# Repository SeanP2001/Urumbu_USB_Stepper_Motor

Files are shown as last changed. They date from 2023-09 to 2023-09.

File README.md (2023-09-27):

# Urumbu USB Stepper Motor

**This Project follows on from the work of Professor Neil Gershenfeld, Quentin Bolsee and Rob Hart at MIT. [Here](https://gitlab.cba.mit.edu/neilg/urumbu) is the original repository.**

## Table of Contents <!-- omit from toc -->

- [Introduction](#introduction)
- [Brief](#brief)
- [Design Aims](#design-aims)
- [PCB Design](#pcb-design)
- [Manufacturing](#manufacturing)
- [Programming](#programming)
  - [Flashing SAMD11 Firmware](#flashing-samd11-firmware)
  - [Adding the Arduino IDE Board Manager](#adding-the-arduino-ide-board-manager)
  - [The Arduino Code](#the-arduino-code)
  - [The Test Code](#the-test-code)
- [Motor Module Characteristics](#motor-module-characteristics)
  - [Current Draw](#current-draw)
  - [Motor Speed](#motor-speed)
  - [Motor Torque](#motor-torque)
- [Using the Module](#using-the-module)
- [Conclusion](#conclusion)
- [Further Work](#further-work)

## Introduction

In the final year of my Bachelors degree I completed a dissertation. This repository is a summary of that work. Included in the repository is all of the information and files to reproduce and use the modules which I designed.

Bangor FabLAB needed to develop methods to teach the Fab Academy curriculum. The curriculum includes two weeks of making machines that move. Students have a very limited time to complete these projects and so they needed a flexible framework which could be used to rapidly prototype motion systems.

Traditional motion systems have all of the components plugged into the controller board. This board has firmware code to control all of the components. While prototyping, it is common to want to add parts like extra motors or switches. With this approach, the controller board must be re-designed, manufactured and programmed. This is time-consuming, creates waste, breaks the creative flow, and requires substantial skills. Students only have one week to do their projects, and this approach is not suitable.

Professor Neil Gershenfeld and his colleagues Quentin Bolsee and Rob Hart have developed a modular solution to this problem called [Urumbu](https://gitlab.cba.mit.edu/neilg/urumbu). These modules are designed to plug into a computer via a USB port. The modules move in response to serial communications from the connected computer. To add more motors to an Urumbu-based machine, the user simply plugs another motor module into the PC and adds it to their code. This is much quicker and does not break the creative flow.

## Brief

I was tasked with equipping the FabLAB to teach the machine building exercises. This involved...
- Adapting the Urumbu design to meet our requirements.
- Manufacturing a set of modules.
- Testing and documenting the module characteristics to understand their capabilities.
- Demonstrating their use through building a motion system. 

## Design Aims

The original design used a DRV8428 motor driver. This motor driver causes the motor to generate noise. This driver is also surface-mount and so if the driver were to fail mid-project, it would be difficult and time-consuning to replace. 

With these issues in mind, I aimed to design a module with the following characteristics:
- Use a silent, user replaceable stepper motor driver (TMC2208, StepStick socketed package).
- Able to be mounted to the back of a NEMA 14 motor.
- Able to be manufactured in the FabLAB using their isolation milling process with FR1 board.

## PCB Design

After three breadboard prototypes and six circuit board revisions I arrived at this design.

The top section is the power section which takes the five volts from the USB connection and steps it down to a stable 3.3 volts for the microcontroller. The main use for the SAMD microcontroller is to interpret the information from the USB data lines and send the correct direction and step signals to the motor driver. The motor driver connects to the four motor pins and pulses them in sequence to advance the motor whenever it receives a step signal.

<p align="center">
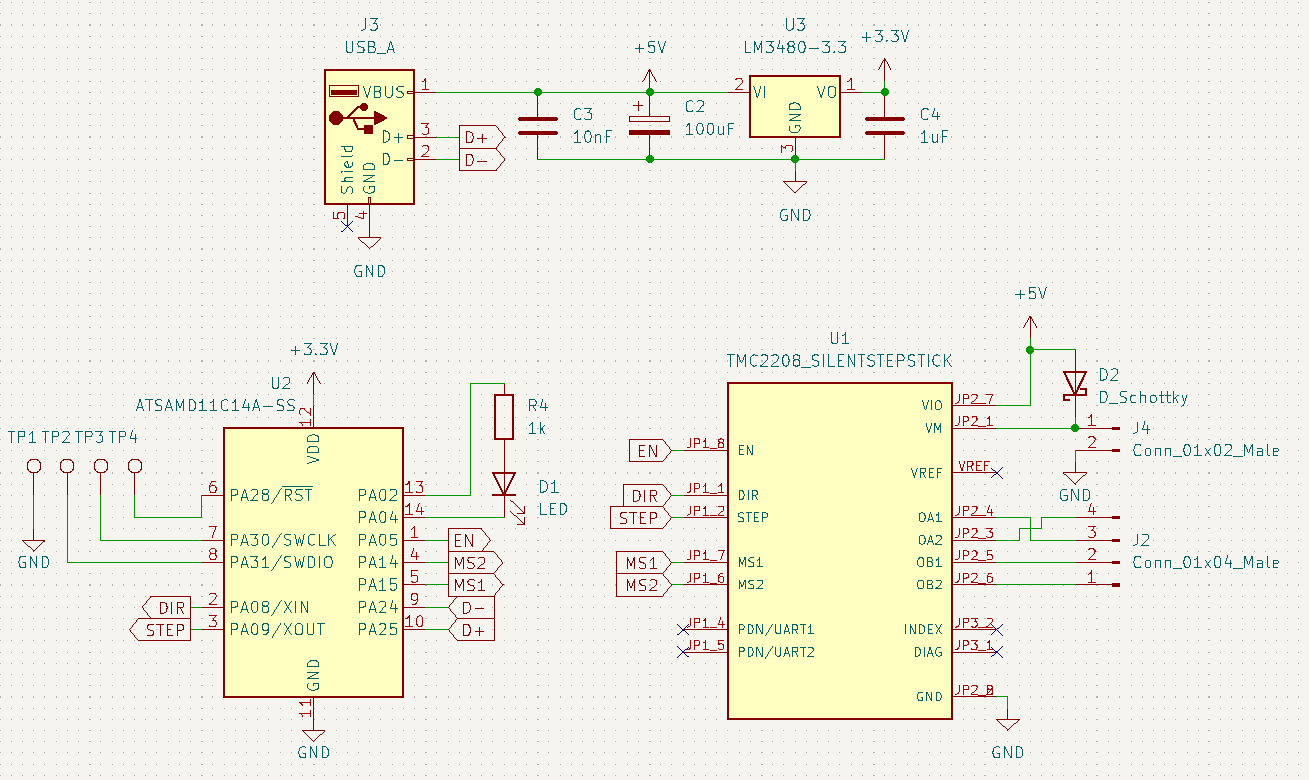
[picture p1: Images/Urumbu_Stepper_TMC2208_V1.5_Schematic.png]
  
</p>

<p align="center">
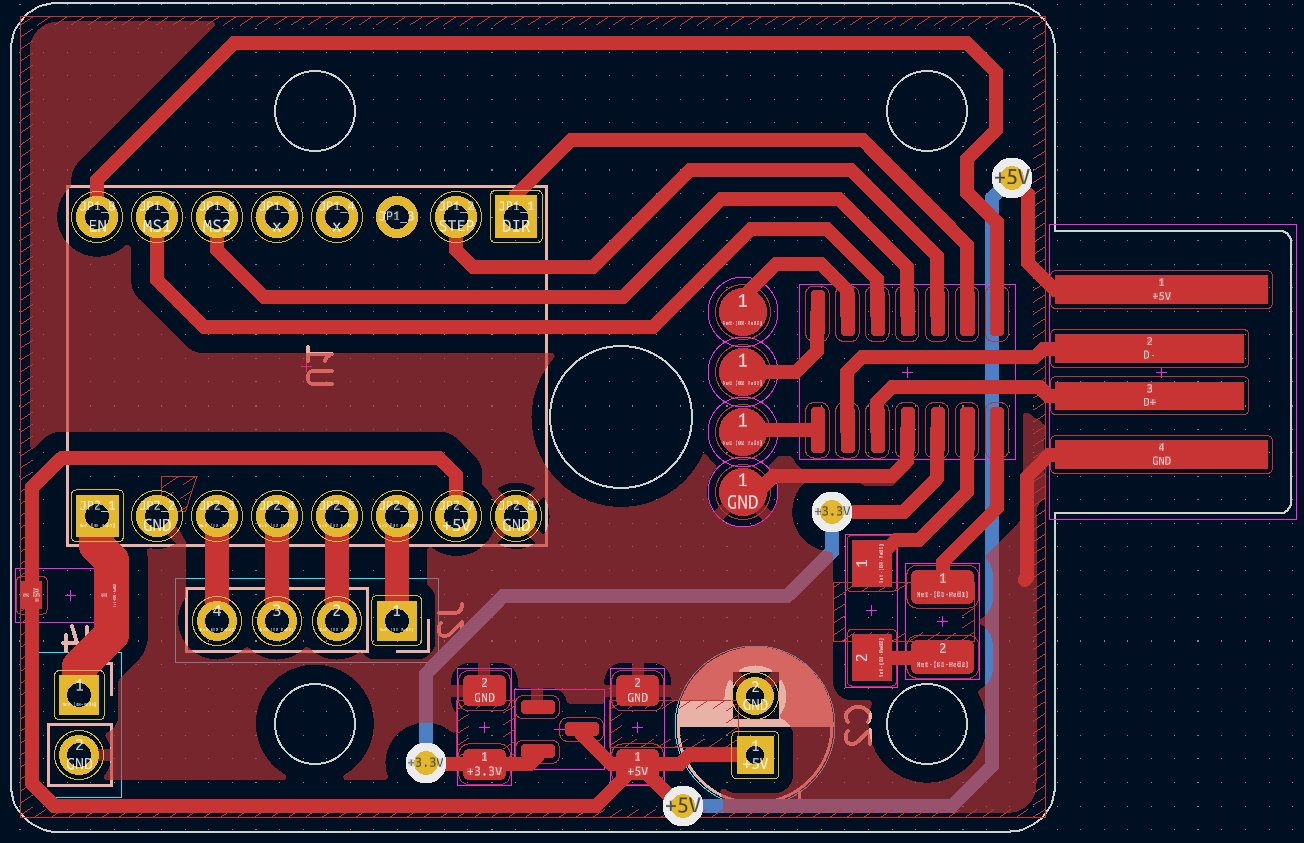
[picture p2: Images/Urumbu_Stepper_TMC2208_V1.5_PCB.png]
  
</p>

## Manufacturing

Images of the PCB were exported from KiCAD. Using [modsproject](https://modsproject.org/), these images were converted into toolpaths and saved in `./PCB_Design/Toolpaths`. Using the Roland SRM-20 CNC mill with a 0.4mm end mill, the traces were isolation milled out of a copper-clad FR1 board. A 0.7mm end mill was then used to drill the holes and cut the board outline. The components were soldered by hand using a soldering iron, as this is the best method for FR1 boards.

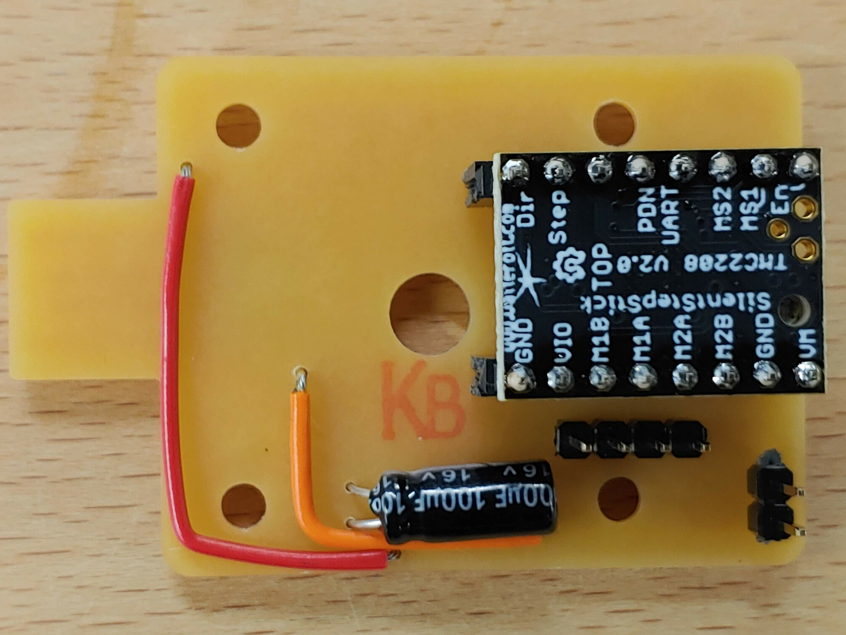
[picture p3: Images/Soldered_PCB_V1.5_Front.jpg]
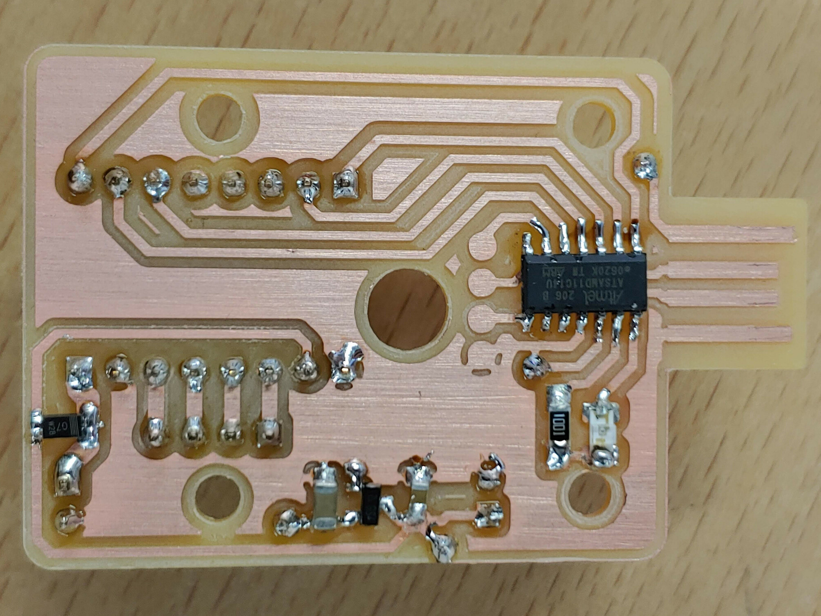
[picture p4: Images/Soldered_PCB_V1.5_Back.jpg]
|   |  |
| --- | --- |

## Programming

### Flashing SAMD11 Firmware

The ["ArduinoCore"](https://github.com/mattairtech/ArduinoCore-samd/blob/master/bootloaders/zero/binaries/sam_ba_Generic_D11C14A_SAMD11C14A.bin) firmware was loaded on to the SAMD11 microcontroller to allow it to be programmed via USB. To do this, I used an Atmel-ICE programmer with the "mini-squid" cable and connected it to the microcontroller in the following way:

| SAM Programming Header Pin Number | Function | SAMD11C Pin Number |
| --- | --- | --- |
| 1 | VREF | 12 |
| 2 | DIO | 8 |
| 3 | GND | 11 |
| 4 | CLK | 7 |
| 5 | GND | 11 |
| 6 | Not Connected | |
| 7 | Not Connected | |
| 8 | Not Connected | |
| 9 | GND | 11 |
| 10 |RST | 6 |

I used a crocodile clip to connect the ground connections to the ground plane. The voltage reference pin was connected via a test clip to the 3V jumper wire on the circuit board. The other connections were connected to a pogo-pin board which was held against the programming pads when the board was being programmed. The board recieved power through the USB connection. 

<p align="center">
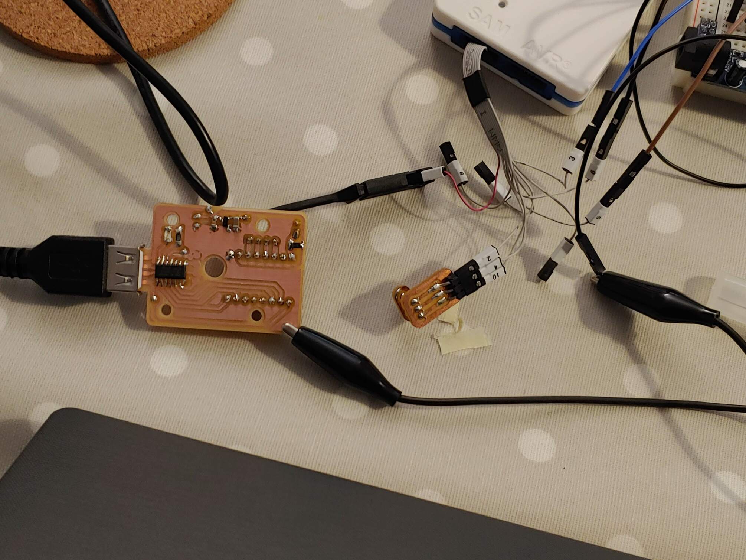
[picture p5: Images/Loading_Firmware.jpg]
  
</p>

Atmel Studio was used to load the firmware onto the microcontroller. While holding the pogo pins to the pads, I selected `Device Programming > Apply` and the device was successfully connected to. On the "Memories" tab I selected the [firmware file](https://github.com/mattairtech/ArduinoCore-samd/blob/master/bootloaders/zero/binaries/sam_ba_Generic_D11C14A_SAMD11C14A.bin) and clicked "Apply" to write the firmware to the microcontroller.

<p align="center">
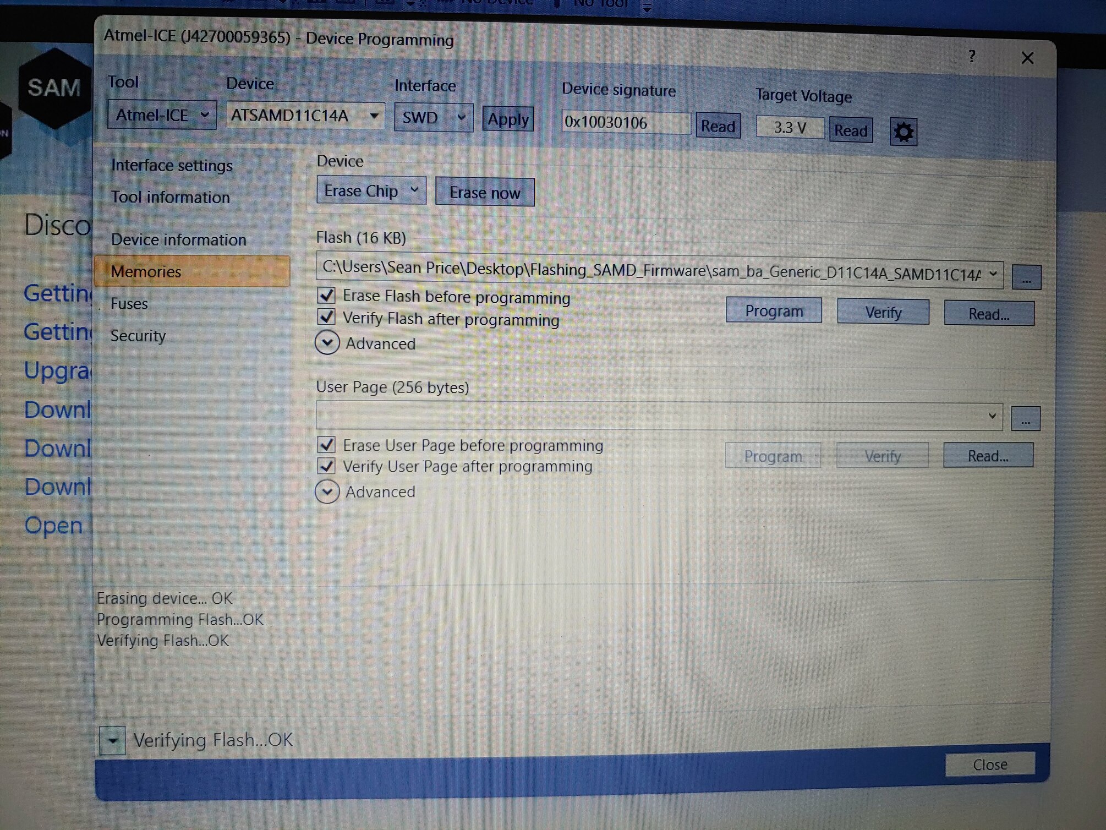
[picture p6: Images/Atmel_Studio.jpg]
  
</p>

### Adding the Arduino IDE Board Manager

The [Fab SAM board manager](https://raw.githubusercontent.com/qbolsee/ArduinoCore-fab-sam/master/json/package_Fab_SAM_index.json) was added to the Arduino IDE, following the [MIT guide](https://mtm.cba.mit.edu/2021/2021-10_microcontroller-primer/fab-arduino/). This allowed the Arduino IDE to be used to program the SAMD11C on the PCB.

### The Arduino Code

The Arduino code running on the Urumbu modules was very heavily inspired by the [original “serialstep” code](https://gitlab.cba.mit.edu/neilg/urumbu/-/tree/master/serialstep/serialstep.ino) used at MIT. The premise of the code is to continuously check whether any serial data has been sent via the USB connection. If the received data is an ’f’, the stepper motor will step clockwise (forwards). If the received data is an ’r’, the stepper motor will step anti-clockwise (reverse).

<p align="center">
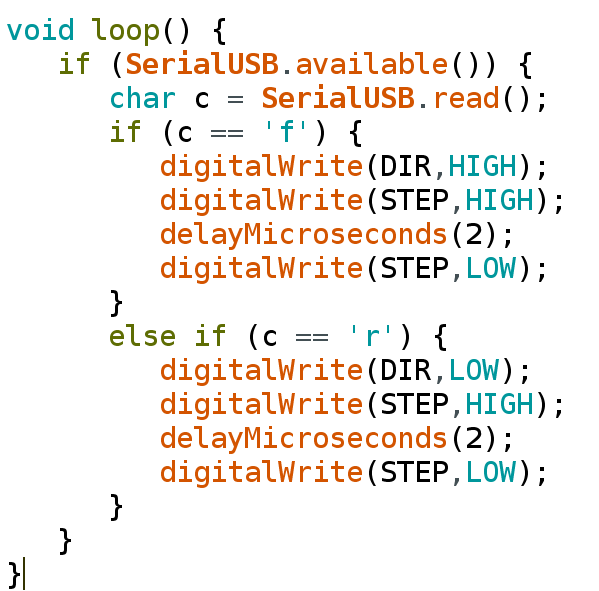
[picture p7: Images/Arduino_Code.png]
  
</p>

### The Test Code

The `./Test_Code/SerialStepControllerTest.py` code sends 'f' and 'r' characters via USB to the motor module to turn the shaft one rotation clockwise and then anti-clockwise repeatedly.

<p align="center">
  
</p>

The `./Test_Code/SerialStepKeyboardControllerTest.py` code sends 'f' and 'r' characters via USB to the motor module to turn the shaft in response to the user pressing the arrow keys on the PC.

<p align="center">
  
</p>

## Motor Module Characteristics

These documented characteristics should help anybody aiming to use these modules by giving them the information to assess whether these modules are capable of fulfilling their requirements.

### Current Draw

| Motor State | Lowest Current Draw (A) | Highest Current Draw (A) | Average Current Draw (A) | 
| --- | --- | --- | --- |
| Idle | 0.13 | 0.19 | 0.16 |
| Moving | 0.31 | 0.37 | 0.34 |
| Moving with 5Ncm Load | 0.31 | 0.37 | 0.34 |

### Motor Speed

The maximum speed of the motor is approximately 2.64 revolutions per second or 158.5 revolutions per minute.

### Motor Torque

The motor was able to lift a mass of 100g at a distance of 6.8cm from the motor shaft. This gives a torque figure of 6.67Ncm.

## Using the Module

I then went on to demonstrate the use of these modules and test that they functioned as expected. To do this I designed, manufactured and programmed a crane motion system. [Here](https://github.com/SeanP2001/Urumbu_Crane) is the repository for that project.

<p align="center">
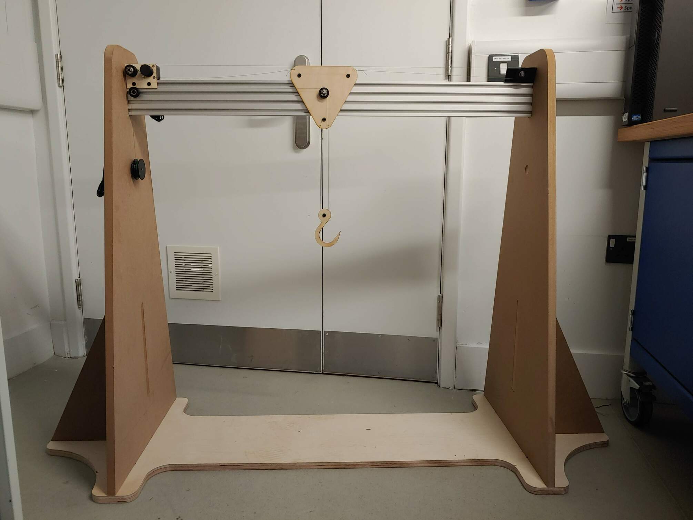
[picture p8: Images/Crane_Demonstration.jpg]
  
</p>

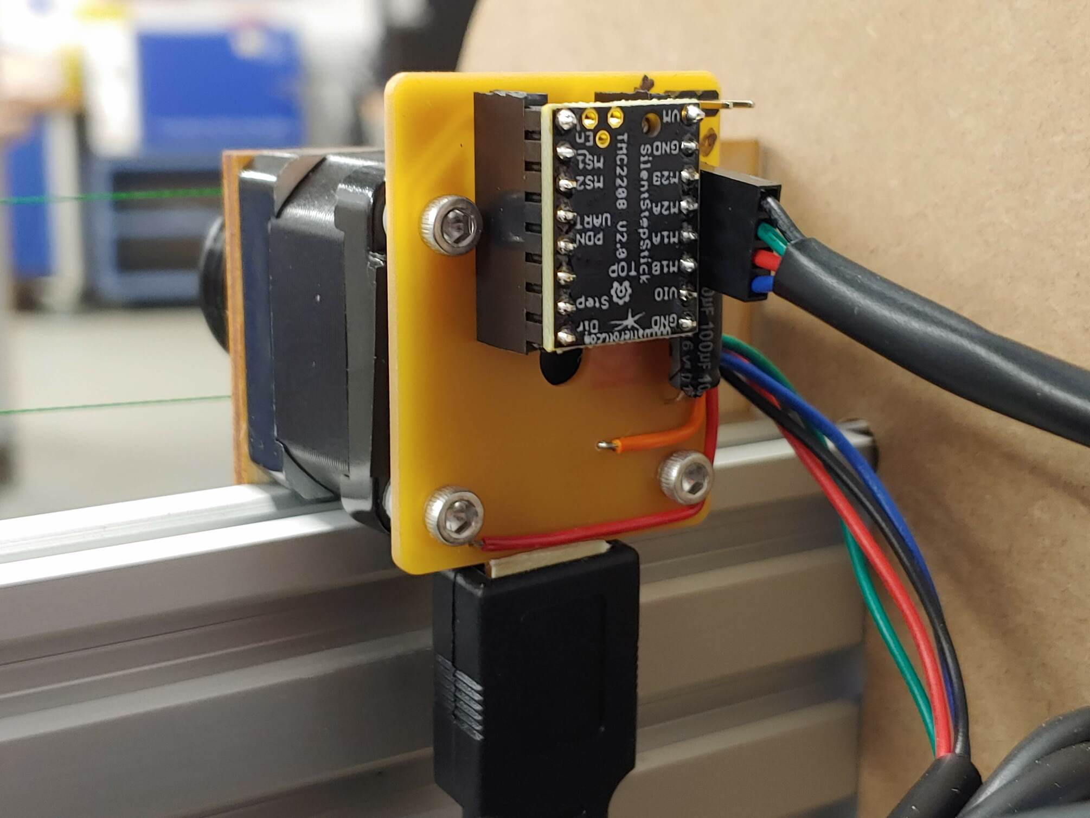
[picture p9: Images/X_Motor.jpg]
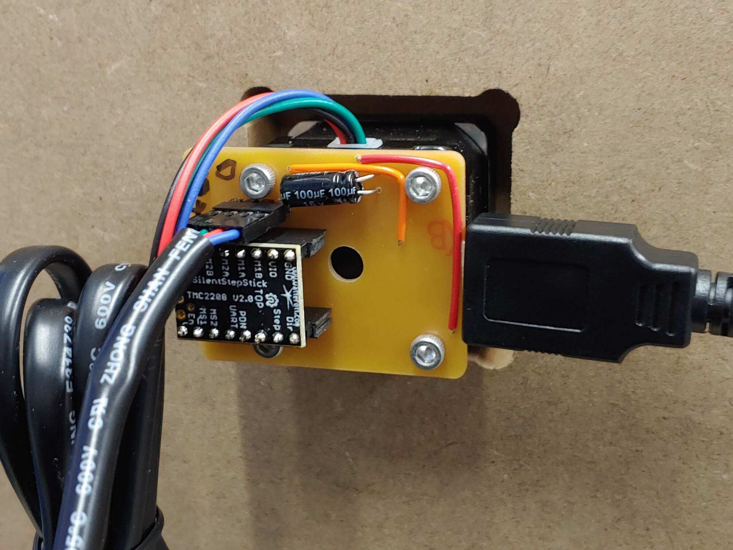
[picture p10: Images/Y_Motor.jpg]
|   |  |
| --- | --- |

## Conclusion

In conclusion, I designed a set of stepper motor Urumbu modules to use a silent, user-replaceable motor driver. A set of modules was manufactured using standard FabLAB tools and parts. The current draw, speed and torque of the motor modules were tested and documented for future students to reference. I also designed and built a motion system to demonstrate the use of these modules. Overall this project was a success. The modules met the brief and will soon be used by Fab Academy students.

## Further Work

There are a few aspects of this project which could be furnter developed:
- Design more modules
  - Button Interface (Controller)
  - Limit Switch
  - LCD
- Write a Python Library to simplify the controller code that students need to write. They could use simple functions to control the modules, rather than dealing with the specifics of the serial communications and distance calculations.

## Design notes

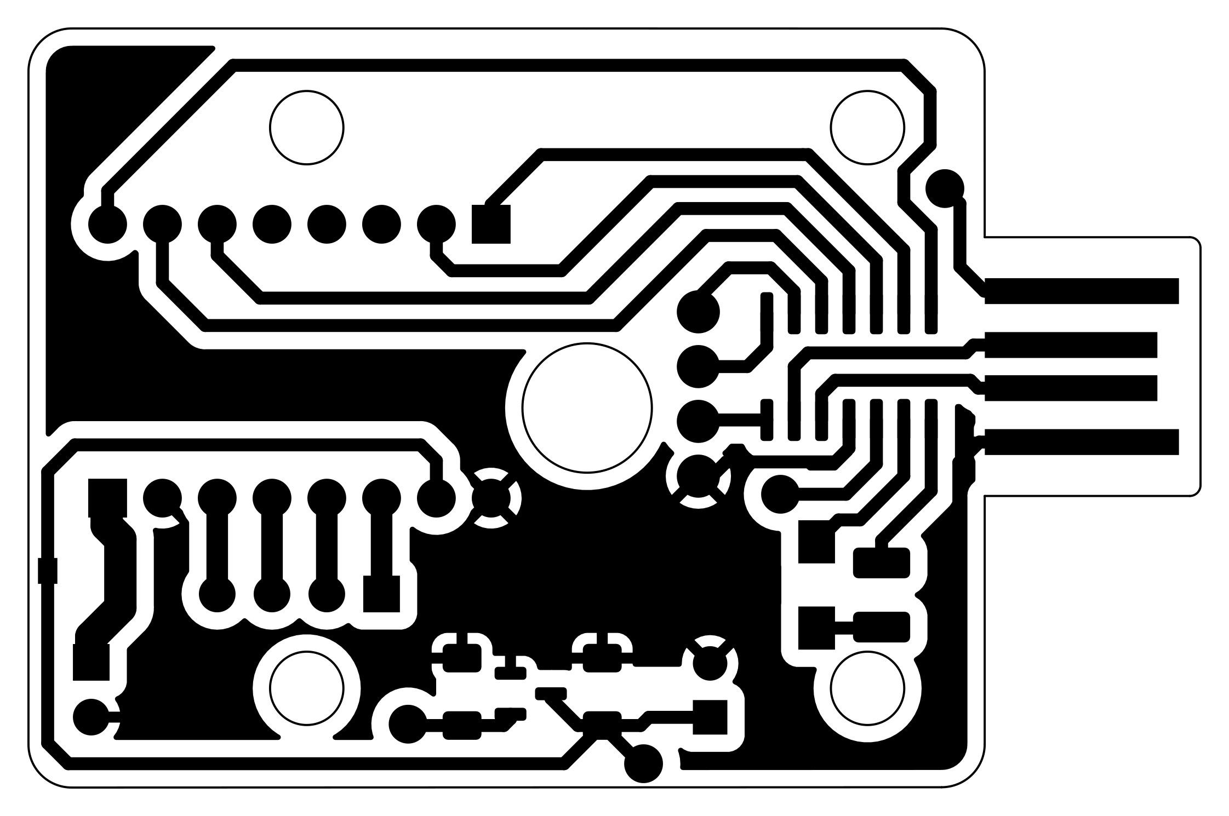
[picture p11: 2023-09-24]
PCB_Design/SVG_Out/Urumbu_Stepper_TMC2208-F_Cu.png

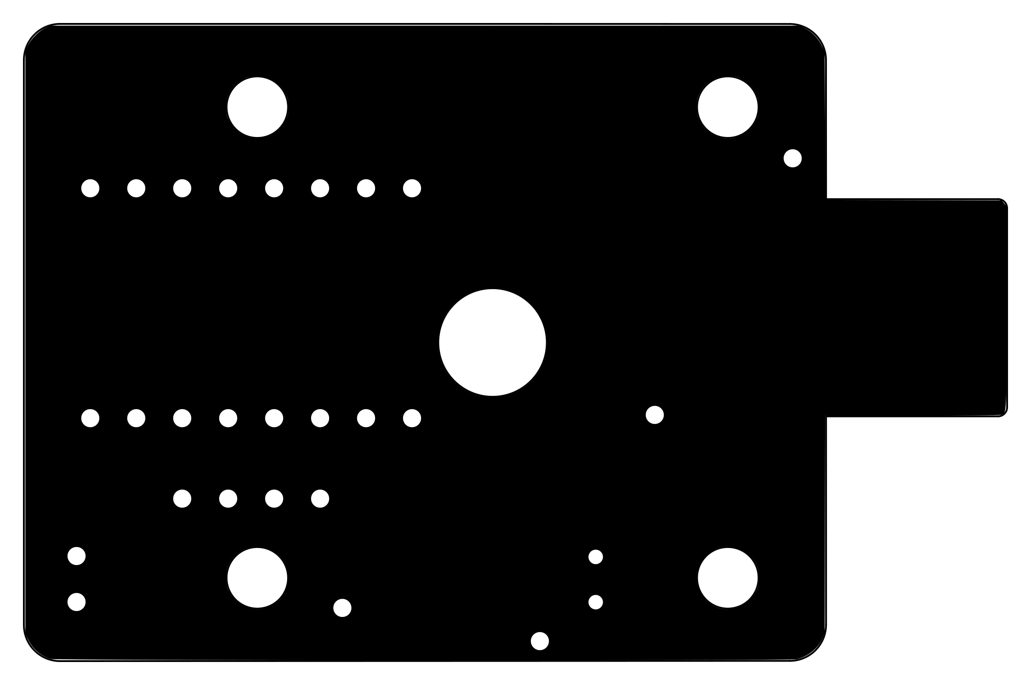
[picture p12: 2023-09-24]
PCB_Design/SVG_Out/Urumbu_Stepper_TMC2208-Edge_Cuts.png

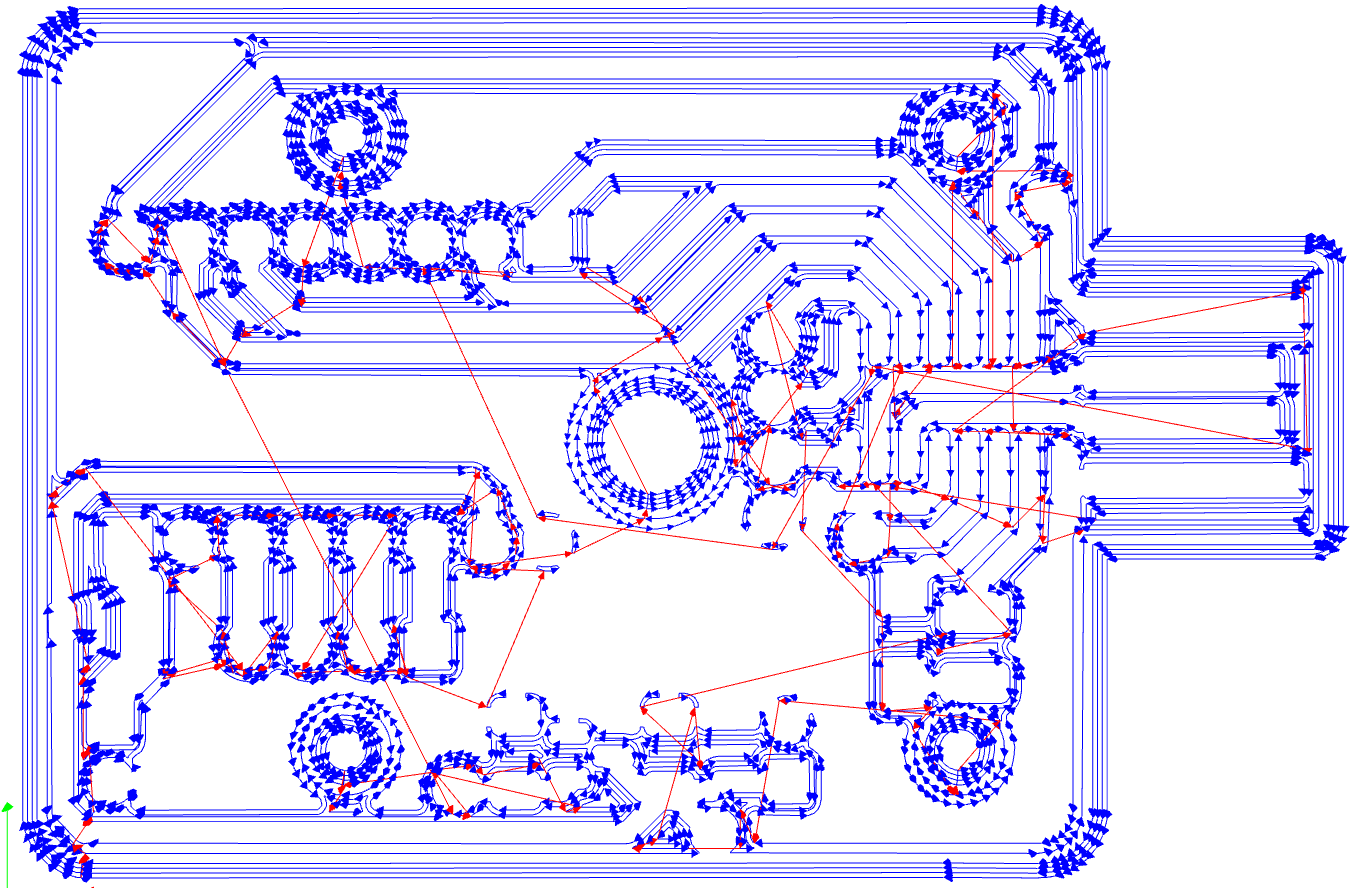
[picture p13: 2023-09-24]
Images/Traces_Toolpath.png

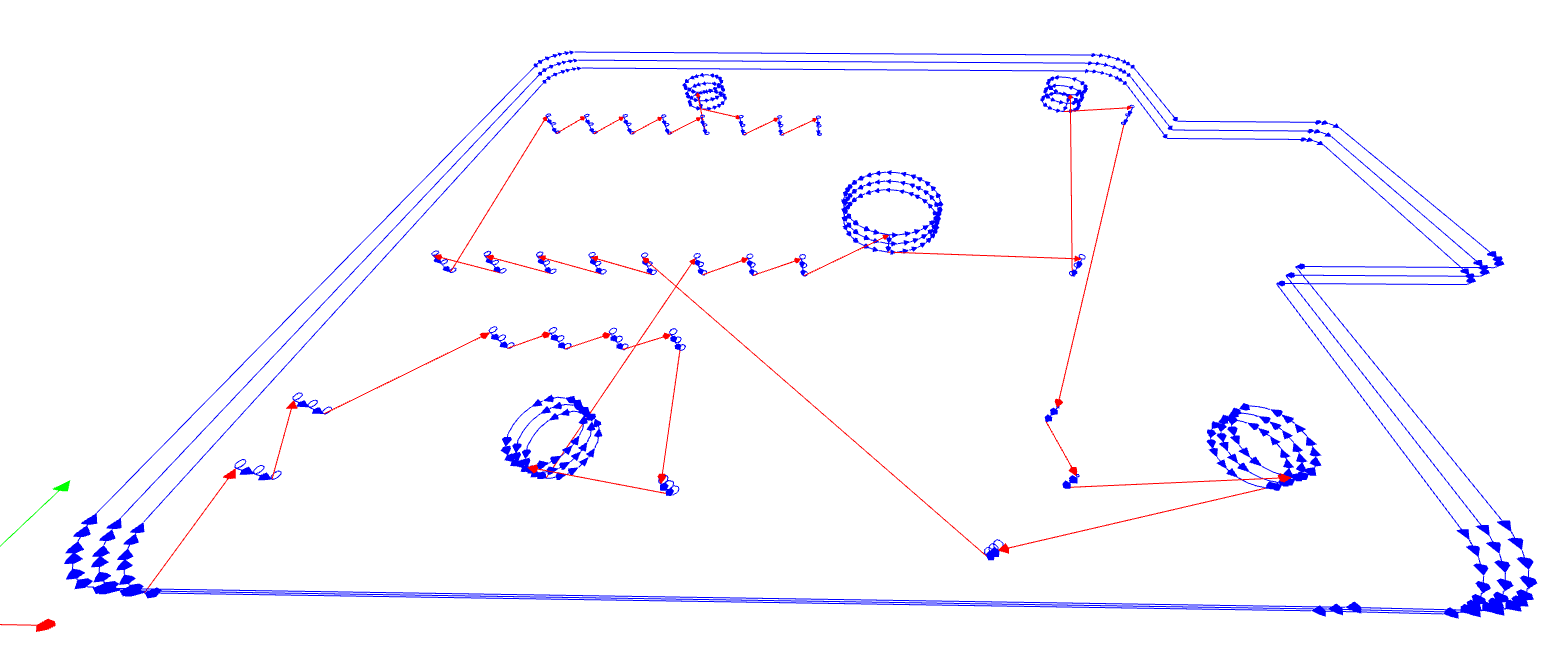
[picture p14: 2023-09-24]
Images/Edge_Cuts_Toolpath.png

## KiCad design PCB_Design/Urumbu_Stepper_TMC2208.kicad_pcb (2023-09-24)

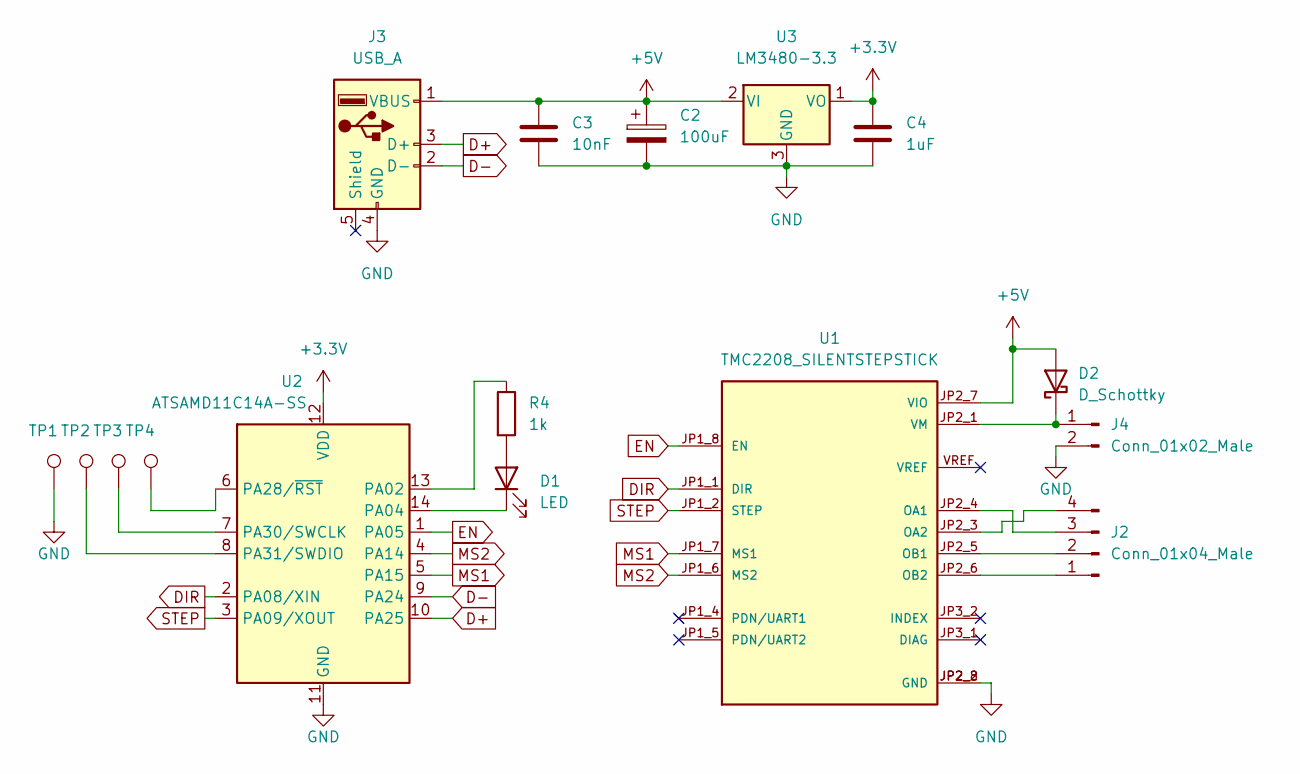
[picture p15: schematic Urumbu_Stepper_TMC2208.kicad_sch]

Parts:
C2: 100uF; CP_Radial_D6.3mm_P2.50mm
C3: 10nF; C_1206_3216Metric_Pad1.33x1.80mm_HandSolder
C4: 1uF; C_1206_3216Metric_Pad1.33x1.80mm_HandSolder
D1: LED; LED_1210_3225Metric_Pad1.42x2.65mm_HandSolder
D2: D_Schottky; D_SOD-123
J2: Conn_01x04_Male; PinHeader_1x04_P2.54mm_Vertical
J3: USB_A; Conn_USB_A_Plain
J4: Conn_01x02_Male; PinHeader_1x02_P2.54mm_Vertical
R4: 1k; R_1206
TP1, TP2, TP3, TP4: TestPoint; TestPoint_Pad_D2.0mm
U1: TMC2208_SILENTSTEPSTICK; TMC2208
U2: ATSAMD11C14A-SS; SOIC-14_3.9x8.7mm_P1.27mm
U3: LM3480-3.3; SOT-23_N_Package

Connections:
+3.3V: C4.1, U2.12 (VDD), U3.1 (VO)
+5V: C2.1, C3.1, D2.2 (A), J3.1 (VBUS), U1.JP2_7 (VIO), U3.2 (VI)
D+: J3.3 (D+), U2.10 (PA25)
D-: J3.2 (D-), U2.9 (PA24)
DIR: U1.JP1_1 (DIR), U2.2 (PA08/XIN)
EN: U1.JP1_8 (EN), U2.1 (PA05)
GND: C2.2, C3.2, C4.2, J3.4 (GND), J4.2, TP1.1, U1.JP2_2 (GND), U1.JP2_8 (GND), U2.11 (GND), U3.3 (GND)
MS1: U1.JP1_7 (MS1), U2.5 (PA15)
MS2: U1.JP1_6 (MS2), U2.4 (PA14)
unnamed: D1.1 (K), U2.14 (PA04)
unnamed: D1.2 (A), R4.2
unnamed: D2.1 (K), J4.1, U1.JP2_1 (VM)
unnamed: J2.1, U1.JP2_6 (OB2)
unnamed: J2.2, U1.JP2_5 (OB1)
unnamed: J2.3, U1.JP2_4 (OA1)
unnamed: J2.4, U1.JP2_3 (OA2)
unnamed: R4.1, U2.13 (PA02)
unnamed: TP4.1, U2.6 (PA28/~RST)
unnamed: TP3.1, U2.7 (PA30/SWCLK)
unnamed: TP2.1, U2.8 (PA31/SWDIO)
STEP: U1.JP1_2 (STEP), U2.3 (PA09/XOUT)

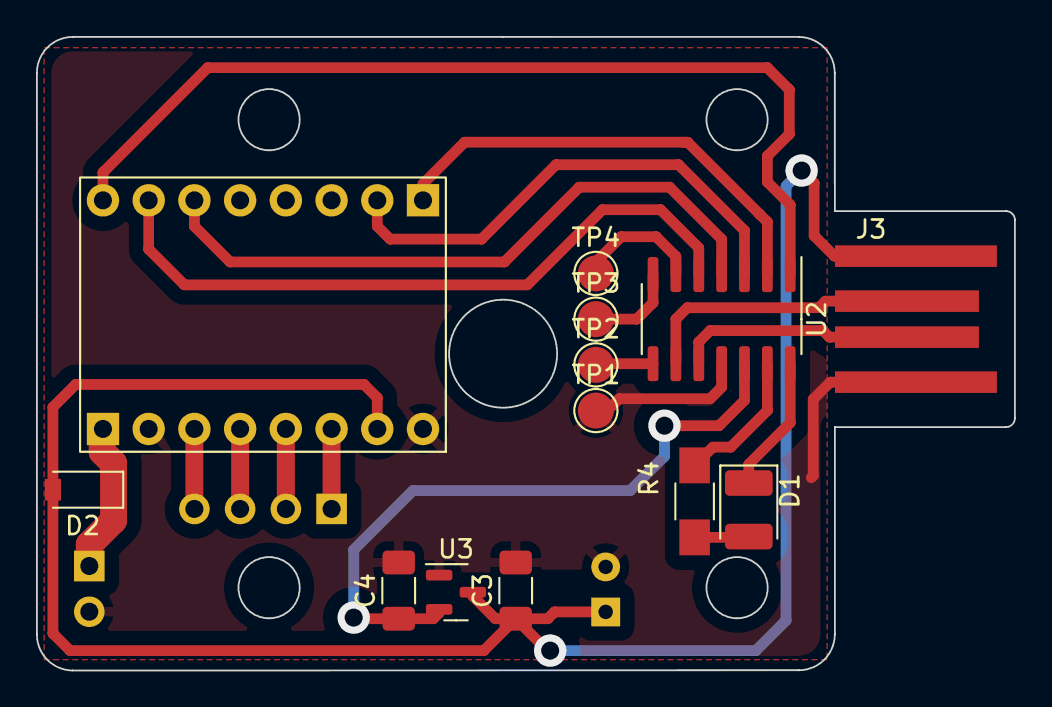
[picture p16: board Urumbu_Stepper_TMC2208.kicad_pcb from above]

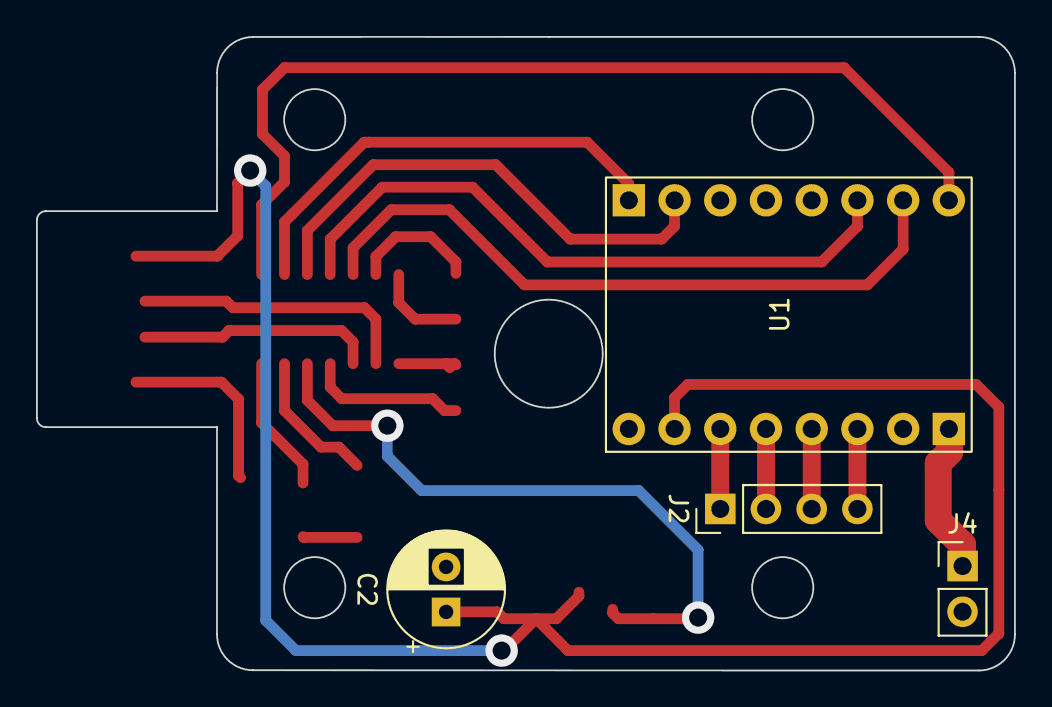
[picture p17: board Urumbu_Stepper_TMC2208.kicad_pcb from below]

Board: 2 copper layers, 54.3 x 35.2 mm, 16 parts (4 on the bottom side), 21 nets.

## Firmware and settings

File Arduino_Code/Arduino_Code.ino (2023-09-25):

//
// This code is a lightly modified version of the original 
// code written by Neil Gershenfeld and Quentin Bolsee.
//
// Original code available here: 
// https://gitlab.cba.mit.edu/neilg/urumbu/-/tree/master/serialstep/serialstep.ino
//
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

#define LEDA 2
#define LEDC 4
#define EN 5
#define DIR 8
#define STEP 9
#define M1 14
#define M0 15
#define NSTEPS 1000
#define DELAYHIGH 10
#define DELAYLOW 1000
#define BLINK 100
#define BUTTON 31

void setup() {
   SerialUSB.begin(9600);
   digitalWrite(LEDA,HIGH);
   pinMode(LEDA,OUTPUT);
   digitalWrite(LEDC,LOW);
   pinMode(LEDC,OUTPUT);
   digitalWrite(EN,LOW);
   pinMode(EN,OUTPUT);
   digitalWrite(STEP,LOW);
   pinMode(STEP,OUTPUT);
   digitalWrite(DIR,LOW);
   pinMode(DIR,OUTPUT);
}

void loop() {
   if (SerialUSB.available()) {
      char c = SerialUSB.read();
      if (c == 'f') {
         digitalWrite(DIR,HIGH);
         digitalWrite(STEP,HIGH);
         delayMicroseconds(2);
         digitalWrite(STEP,LOW);
      }
      else if (c == 'r') {
         digitalWrite(DIR,LOW);
         digitalWrite(STEP,HIGH);
         delayMicroseconds(2);
         digitalWrite(STEP,LOW);
      }
   }
}

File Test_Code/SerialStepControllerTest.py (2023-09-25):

#
# Based on:
# https://gitlab.cba.mit.edu/neilg/urumbu/-/blob/master/serialstep/serialstep.1.py 
#
# This program connects to a stepper motor Urumbu module and controls it.
# The motor will continuously rotate 1 full revolution clockwise and then back again 

import serial,sys,time,signal

if (len(sys.argv) != 4):                                       # If the incorrect number of arguments is given
   print("command line: serialstep.1.py port speed delay")     # Print a help message to the terminal
   sys.exit()                                                  # and exit the program
   
device = sys.argv[1]                                           # Argument 1 is the port of the device (e.g. '/dev/ttyUSB0')
baud = int(sys.argv[2])                                        # Argument 2 is the baud rate of the device (e.g. '9600')
delay = float(sys.argv[3])                                     # Argument 3 is the delay between steps in seconds (e.g. '0.001')

print('open '+device+' at '+str(baud)+' delay '+str(delay))    # Print to the console to show the user request
port = serial.Serial(device,baudrate=baud,timeout=0)           # connect to the serial port

print('Serial Port Opened')

#---------------------------------------------------------------------------------------------------------------------------------

count = 0                                                      # total number of steps
stepsPerRevolution = 1600                                      # total number of steps per revolution
forward = b'f'                                                 # send 'f' to drive the motor forward/clockwise
reverse = b'r'                                                 # send 'r' to drive the motor reverse/anti-clockwise

#---------------------------------------------------------------------------------------------------------------------------------
while(1):                                                      # loop until the program is terminated
    
   while (count < stepsPerRevolution):                         # loop until a full clockwise revolution has been completed
      port.write(forward)                                      # send an 'f' to the Urumbu device to rotate 1 step clockwise        
      print("Forward")
      count += 1                                               # add 1 to the step count
      time.sleep(delay)                                        # wait the specified time (in seconds)
      
   while (count < stepsPerRevolution*2):                       # loop until a full anti-clockwise revolution has been completed
      port.write(reverse)                                      # send an 'r' to the Urumbu device to rotate 1 step anti-clockwise
      print("Reverse")
      count += 1                                               # add 1 to the step count
      time.sleep(delay)                                        # wait the specified time (in seconds)
      
   count = 0                                                   # reset the step count before looping
